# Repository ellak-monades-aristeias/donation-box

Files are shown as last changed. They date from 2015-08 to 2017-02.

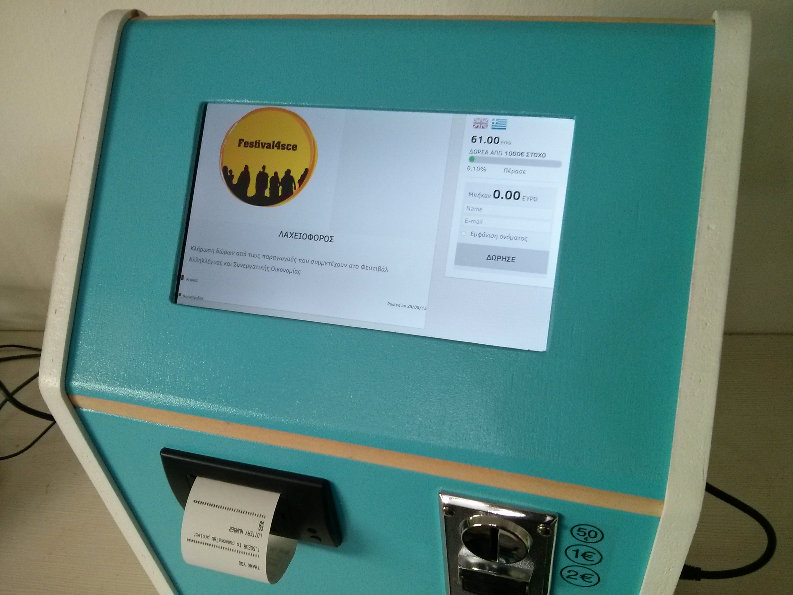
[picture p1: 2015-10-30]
info/photos/inuse/PrintedReceipt.jpg

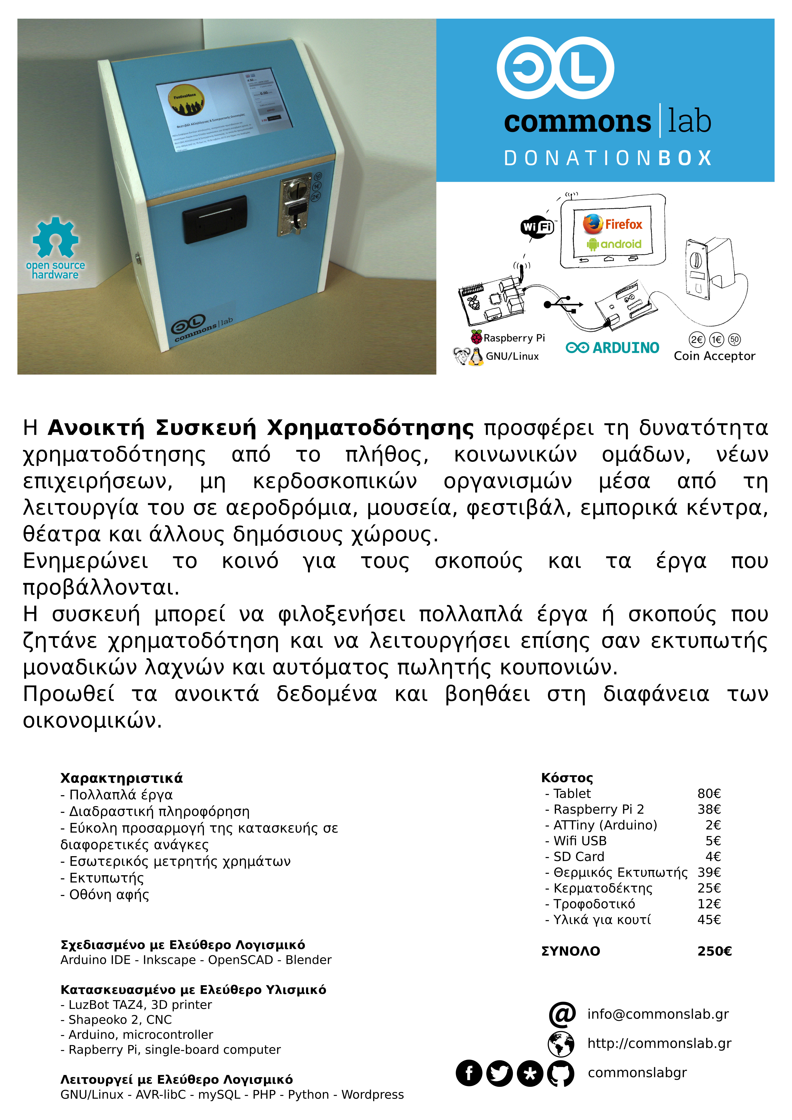
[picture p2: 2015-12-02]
info/Poster-el.jpg

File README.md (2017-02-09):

donation-box
============

open source design/ open source hardware/ open source software

Note: The process of how to set up your own donation box is still under heavy development and the documentation not complete or detailed enough yet. If you are anyhow interested in building and setting up your own box and you can't wait, don't hesitate to contact us.

##Idea
During the last few years, especially in Greece, many communities and initiatives have tried to do things in many different fields of interest. Often times, these teams will sooner or later need some funding in order to fulfill their goals. Some of them organize events, some run online crowdfunding campains and some also find several new ways to cover their needs.
From our experience, online crowdfunding does not work as expected, most of the time. People are hesitating to put all their details online, especially if they choose to donate a small amount, or some may not have a debit or credit card to do that. Eventually, most of these people prefer to give their donations in cash, in person or into a physical box somewhere. Of course, many donation boxes, usually managed by NGOs, already exist in public places, shops and such places. The problem with these boxes is that they do not offer much information about the organization that asks for money, nor do they offer transparency about what happens to the donations, who are the organization, or how much money they need.
Due to the lack of possible ways to convey sufficient information, traditional donation boxes are not being used by teams that focus on a specific project, because people can not understand what the project exactly is.
In order to solve the above problems, we came up with the idea of a screen-enabled interactive donation box.
The box can run several projects or causes that are asking for donations. It provides information (text, images, video) for each project. It provides real-time information about the progress (donations accepted, donations needed, finishing date). Donations are recorded and if users choose so, they can be registered to keep in touch with the project for which they donated.
The box also can issue receipts for each donation.
Connecting several donation boxes to an online service can add more value to each box and all the projects that are running, as a project can be created online and activated in several boxes in several locations simultaneously.
This way, we hope to help NGOs, social initiatives and others, to achieve their goals and their fulfil their ideas. By offering a platform for crowdfunding that exists in physical, public spaces, we are offering a different and more direct connection between projects asking for help and people willing to help.

##Description
An open-source screen enabled donation box

The software has three items. 
* The Serial2DB which is a simple deamon written in python which listens on the serial port for messages from the Arduino which is connected to the coin acceptor and writes all entries to an SQL DB.
* The wsServer which is a WebSocket server written in python which reads the SQL DB for new entries and then notifies any connected websocket clients of these. Additionally listens for any donations made and alters accordingly the SQL DB.
* The Wordpress widgets and theme customizations. Which are used for offering an improved user experience based on the design assumption that the wordpress site is running on a 10" tablet. The theme is currently based on Influence and there are several widgets developed to enhance the sidebar. Several plug ins needed for the current implementation and features are already under the plugins folder.

##Setup
###Hardware
The current development is based on the initial following design:
  *A programmable coint acceptor
  *Arduino compatible, connected to the coin acceptor and translating the readings to something more readable (e.g. EUR|2.00)
  *A Raspberry Pi connected through serial to the Arduino and running this software.
  *A tablet that connects through WiFi to the Raspberry Pi (that acts as a hot spot) and loads the Wordpress site.

###Installation
####Arduino
The code for the Arduino to read the coin acceptor will be uploaded soon...

####Raspberry Pi

* Set up DHCP
* Set up DNS
* Set up WiFi access point
* Set up IP forwarding
* Install python tornado
* [Printer] sudo apt-get install python-serial python-imaging python-unidecode
* Copy repository and start Serial2DB & wsServer.

* Install lighthttpd
* Install MySQL
* Create custom DB tables. Run the create_tables.sql
* Install PHP
* Set up Wordpress
* Add Influence theme 
* Add included child theme & plugins
* Import widgets 

####Android Tablet
* Install Firefox
* Connect to WiFi running on the Pi.
* Load home page
##Developers
More detailed [Developers Manual](DevelopersManual.md).

##Users
More detailed [Users Manual](UserManual.md).

Developed by CommonsLab

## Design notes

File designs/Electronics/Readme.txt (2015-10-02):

DonationBox.fzz
Contains the electronics schematic for the custom Raspberry Pi shield.
To open it you will need Fritzing - http://fritzing.org

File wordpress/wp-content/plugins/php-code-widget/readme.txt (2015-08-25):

=== PHP Code Widget ===
Contributors: Otto42
Donate link: https://www.paypal.com/cgi-bin/webscr?cmd=_donations&business=otto%40ottodestruct%2ecom
Tags: php, widget, execphp
Requires at least: 2.8
Tested up to: 4.3
Stable tag: 2.3
License: GPLv2
License URI: http://www.opensource.org/licenses/GPL-2.0

Like the Text widget, but also allows working PHP code to be inserted.

== Description ==

The normal Text widget allows you to insert arbitrary Text and/or HTML code. This allows that too, but also parses any PHP code in the text widget and executes it. 

This can make it easier to migrate to a widget-based theme. However, this plugin should not be used long term, as anybody with access to edit the widgets on your site will be able to execute arbitrary PHP code.

All PHP code must be enclosed in the standard php opening and closing tags ( `<?php` and `?>` ) for it to be recognized and executed.

Only users with the unfiltered_html role will be allowed to insert unfiltered HTML. This includes PHP code, so users without admin or editor permissions will not be able to use this to execute code, even if they have widget editing permissions.

== Frequently Asked Questions ==

= There's some kind of error on line 26! =

That error means that your PHP code is incorrect or otherwise broken. 

= But my code is fine! =

No, it's not. Really. 

This widget has no real errors in it, it's about the simplest widget one can possibly make. Any errors coming out of the "execphp.php" file are errors in code you put into one of the widgets. The reason that it shows the error being in the execphp.php file is because that is where your widget's code is actually being run.

So, if it says that you have an error on line 26, I assure you, the problem is yours. Please don't email me about that error.

= I have code that works normally in a template but doesn't work when in the widget? =

Code in a template runs in the global context. Code in the widget will run in a function context. Make sure that you declare any global variables as global before attempting to use them.

== Screenshots ==

1. The widgets screen showing a PHP code widget in use.
2. The output of the widget on the site.

== Changelog ==

= 2.3 =
* Changed the call to WP_Widget to use the PHP 5 __construct() method. Ref: https://make.wordpress.org/core/2015/07/02/deprecating-php4-style-constructors-in-wordpress-4-3/

= 2.2 =
* Translation fixes for WP 3.7
* Remove donation link

= 2.1 =
* Fixed broken wpautop filter. Checkbox on widget works now.

= 2.0 =
* Changed widget to use new Class methods for creating widget. This simplifies the widget and should eliminate any problems with it losing code or disappearing from sidebars and so forth.

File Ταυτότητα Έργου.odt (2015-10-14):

Ανοικτή Συσκευή Χρηματοδότησης Donation Box

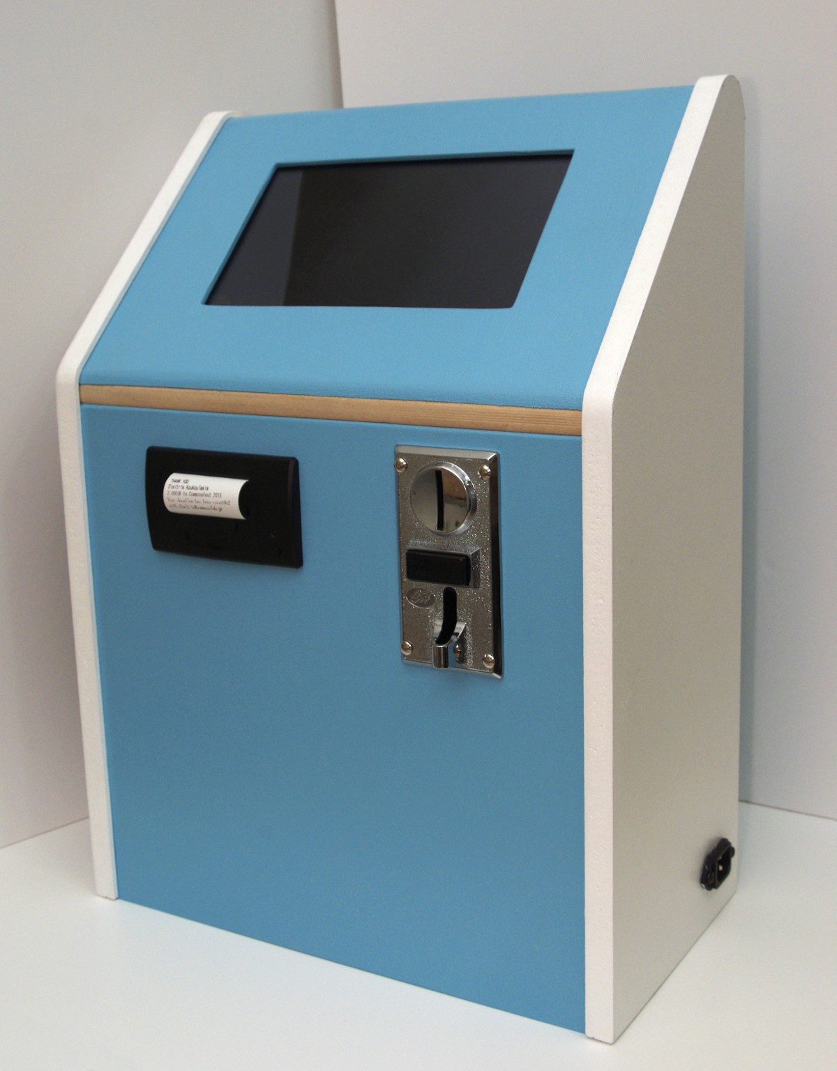
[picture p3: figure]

# Περιγραφή

Η Ανοικτή Συσκευή Χρηματοδότησης δίνει τη δυνατότητα χρηματοδότησης σε ομάδες και έργα μέσα από τη προβολή τους σε δημόσιους φυσικούς χώρους. Μπορεί να παρέχει πληροφορίες για κάθε ομάδα και έργο που ζητάει χρηματοδότηση, να δέχεται και να καταγράφει τα νομίσματα που δίνονται, να εκτυπώνει απόδειξη και να ενημερώνει τους χρήστες για τη πορεία χρηματοδότησης του κάθε έργου σε πραγματικό χρόνο.

# Χρήση

Η Ανοικτή Συσκευή Χρηματοδότησης έχει σκοπό τη διάδοση και υλοποίηση της ιδέας της χρηματοδότησης έργων από το πλήθος (crowdfunding) σε φυσικούς χώρους.

Η συσκευή μπορεί να εγκατασταθεί σε δημόσιους χώρους όπως μουσεία, πολιτιστικά κέντρα, καφετέριες, μεζεδοπωλεία, εμπορικά κέντρα, κοινωνικούς χώρους, αεροδρόμια κ.α.

Ο χρήστης μπορεί να επιλέγει τα έργα που θα εμφανίζονται για χρηματοδότηση και να κρατάει ένα ποσοστό αν έχει συμφωνηθεί για τη συντήρηση της συσκευής. Επίσης ο χρήστης ή κάποιος τρίτος να φροντίζει για τη σωστή διανομή των χρημάτων όπως θα έχει συμφωνηθεί. Τα ανοιχτά δεδομένα από τις συσκευές μπορούν να δημοσιεύονται στο διαδίκτυο ώστε μέσω της διαφάνειας να εξασφαλίζετε η διαδικασία.

# Υλικά

### Ξύλα

### Βίδες κ.α.

### Ηλεκτρονικά

ΣΥΝΟΛΟ 307,32 €

# Αποθετήριο

https://github.com/ellak-monades-aristeias/donation-box

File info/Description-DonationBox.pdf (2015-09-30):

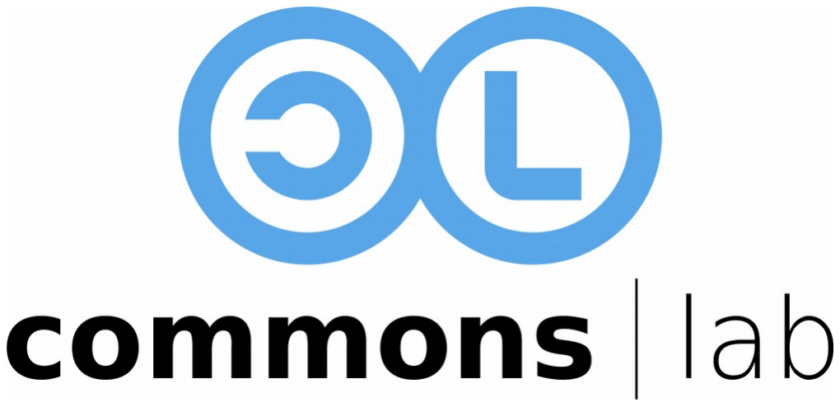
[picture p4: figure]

# Δίκτυο ανοικτών συσκευών μικροχρηματοδότησης

## Τεχνικά στοιχεία

Ανοικτός σχεδιασμός της συσκευής. Εύκολη αναπαραγωγή του και διαμόρφωση για να καλύψει τις ανάγκες σε διαφορετικούς χώρους.
Προσφέρει βασική ασφάλεια για τη συσκευή να βρίσκεται σε εσωτερικό δημόσιο χώρο. Περιλαμβάνει:
- ενα προγραμματιζόμενο κερματοδέκτη, για τουλάχιστον 3 διαφορετικά νομίσματα (0.50, 1.00 & 2.00 €)
- ένα μικροελεγκτή συμβατό με το Arduino
- ένα Raspberry Pi B (ή οποιοδήποτε άλλο Η/Υ που να τρέχει GNU/Linux)
- ένα WiFi usb stick.
- Τροφοδοτικό
- Ταμπλέτα 10”

Δίκτυο συσκευών
Δυνατότητα δημοσίευσης και παρακολούθησης των έργων σε διαδικτιακή εφαρμογή με την οποία επικοινωνούν, ενημερώνουν και ενημερώνονται οι συσκευές χρηματοδότησης σε όποιο σημείο και αν βρίσκονται.

## Σκοπός και χρήση

Η ανοικτή συσκευή οικονομικής ενίσχυσης έχει σαν σκοπό την διάδοση και την υλοποίηση της ιδέας της χρηματοδότησης έργων από το πλήθος (crowdfunding) σε φυσικούς χώρους.

## Υπάρχουσες λύσεις

Η χρηματοδότηση από το πλήθος τα τελευταία χρόνια έχει δώσει την δυνατότητα σε χιλιάδες άτομα, ομάδες, οργανισμούς και επιχειρήσεις από όλο τον κόσμο να έχουν πρόσβαση σε χρηματικά κεφάλαια προκειμένου να υλοποιούν πάσης φύσεως έργα.

Αυτό επιτυγχάνεται μέσα από διάφορες ηλεκτρονικές πλατφόρμες οπού οι ενδιαφερόμενοι παρουσιάζουν τις ιδέες τους στο κοινό και ζητάνε συγκεκριμένα ποσά για την υλοποίηση τους. Οι χρηματοδότες με την χρήση λογαριασμών PayPal ή χρεωστικών και πιστωτικών καρτών ενισχύουν οικονομικά τα διάφορα έργα.
Την ίδια στιγμή σε δημόσιους χώρους υπάρχουν κουτιά οικονομικής ενίσχυσης που τοποθετούν διάφορες ομάδες ή μη κερδοσκοπικές οργανώσεις προκειμένου να ενισχύσουν δράσεις φιλανθρωπικού, καλλιτεχνικού, κοινωνικά αλληλέγγυου κ.α. χαρακτήρα.
Τα συγκεκριμένα κουτιά ενίσχυσης στηρίζονται κατά κύριο λόγο στην εμπιστοσύνη που έχει το πλήθος προς την επωνυμία του κατόχου τους χωρίς όμως να δίνουν οποιαδήποτε άλλη πληροφορία σχετικά με το έργο,την ομάδα, το πόσο που έχει συγκεντρωθεί σε κάθε χρονική στιγμή και το πόσο στόχο.

## Στοιχεία κοινοτομίας, ανάγκες και προβλήματα που επιλύει

Η συσκευή ανοικτής οικονομικής ενίσχυσης έχει σαν στόχο να καλύψει το κενό ανάμεσα στις δυο παραπάνω περιπτώσεις. Δίνοντας την δυνατότητα στους ενδιαφερόμενους:
- Να παρουσιάσουν την ομάδα και το έργο τους μέσα από κείμενα, φωτογραφίες, βίντεο.
- Να παρέχουν πρόσβαση στα οικονομικά δεδομένα του ποσού στόχου και του ποσού που έχει συγκεντρωθεί.
- Να συγκεντρώσουν ποσά που οι ενδιαφερόμενοι μικροχρηματοδότες δεν θα έδιναν σε πλατφόρμες crowdfunding λόγω της διαδικασίας υποβολής των προσωπικών στοιχείων που απαιτούνται.
- Να έχουν πρόσβαση σε ένα μεγαλύτερο δίκτυο συσκευών μικροχρηματοδότησης που εκτείνεται και πέρα από τα γεωγραφικά όρια δράσης τους.
- Να παρέχουν πληροφορίες για την πορεία υλοποίησης του έργου
- Να καλλιεργούν το προφίλ τους μέσα στο ευρύτερο δίκτυο.
- Να κατασκευάσουν μόνοι τους την συσκευή οικονομικής ενίσχυσης κάνοντας χρήση των ελεύθερων αδειών λογισμικού, υλισμικού και σχεδιασμού.

## Οφέλη ανοιχτότητας - Σύντομη τεκμηρίωση της κοινωνικής, περιβαλλοντικής και οικονομικής

βιωσιμότητας της πρότασης.

Το γεγονός ότι η ανοικτή συσκευή οικονομικής ενίσχυσης καλύπτεται από ελεύθερες άδειες λογισμικού, υλισμικου και σχεδίασης έχει τα εξής οφέλη
ως προς την κατασκευή:
1. Την δυνατότητα κατασκευής της από οποιονδήποτε το επιθυμεί.
2. Την δυνατότητα αναβάθμισης, προσαρμογής και βελτίωσης της.
Ως προς την κοινωνική βιωσιμότητα:
1. Την δυνατότητα πρόσβασης σε μικροχρηματοδότηση έργων που δεν μπορούν να χρηματοδοτηθούν με άλλο τρόπο.
2. Με την χρήση ανοικτών δεδομένων ελαχιστοποιείται η πιθανότητα παραπλάνησης όσων θέλουν να ενισχύσουν και την καλλιέργεια σχέσεων εμπιστοσύνης μειώνοντας έτσι τους πόρους που απαιτούνται για το σκοπό αυτό σε μεταγενέστερη πρόταση χρηματοδότησης.
3. Την ενίσχυση της ιδέας της κοινότητας και την παροχή δυνατότητας συμμετοχής σε έργα με κοινωνικό όφελος μέσω της χρηματοδότησης από άτομα που δεν έχουν τον χρόνο να συμμετέχουν με άλλο τρόπο.
Ως προς την περιβαλλοντική βιωσιμότητα
- Η κατασκευή της συσκευής μπορεί να γίνει με την χρήση μηχανημάτων μικρής όχλησης χωρίς να απαιτεί ιδιαίτερες εγκαταστάσεις και λόγω των ελεύθερων αδειών της μπορεί να στηριχθεί σε ένα ομότιμο δίκτυο παραγωγής και διαχείρισης σε τοπικό επίπεδο.
Το δίκτυο αυτό θα έχει την δυνατότητα μέσω της χρήσης ήδη τοποθετημένων συσκευών ενίσχυσης να χρηματοδοτεί την κατασκευή και την τοποθέτηση νέων συσκευών δημιουργώντας έτσι τις προϋποθέσεις περαιτέρω επέκτασης του. Ουσιαστικά μια συσκευή έχει την δυνατότητα χρηματοδότησης μιας νέας συσκευής.
- Δίνει την δυνατότητα μείωσης του κόστους κατασκευής και λειτουργίας με την χρήση laptop, tablet, touchscreen, smartphone και δικτύων wifi που υπάρχουν ήδη.

Τέλος η συσκευή ενίσχυσης με την τοποθέτηση της σε δημόσιο χώρο μπορεί να έχει και άλλες χρήσεις εκτός της μικροχρηματοδοτησης όπως:
- Αγορά ψηφιακών νομισμάτων
- Παροχή πάσης φύσεως πληροφορίας
- Διοργάνωση κληρώσεων δώρων
- Αυτόματου πωλητή μέσω κουπονιών
- Παροχή wifi

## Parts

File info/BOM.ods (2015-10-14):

Donation Box Bill of Materials
Items | Description | Notes | Cost | Source
Case
 | MDF | 8mm ca. 1m2 | 8,00 € | Praktiker
 | Plywood | 4mm ca. 1/4m2 | 3,00 € | Praktiker
 | Chipboard | 16mm ca. 1m2 | 8,00 € | Praktiker
 | Power off Button |  | 0,50 € | Local electronics store
 | Hinge | 2x | 4,00 € | Praktiker
 | Screws & Nuts |  | 4,00 € | Local Hardware store
 |  | 40x 3mmx16mm |  | Local Hardware store
 |  | 4x M4 20mm
 |  | 4x M4
 | Angles | 12x | 3,60 €
 | Lock | D19XL22 | 9,00 € | Local Hardware store
Electronics
1 | Raspberry Pi 2 |  | 37,50 € | http://www.reichelt.com/?ARTICLE=152728
1 | Coin Acceptor |  | 25,00 € | http://www.ebay.com/itm/250784120899
1 | Arduino | ATtiny85 | 1,20 € | http://www.reichelt.com/?ARTICLE=69299
1 | Power supplies | 12V 0.5A | 2,00 €
 |  | 9V 1.5A | 2,00 €
 |  | 5V 2A | 2,00 €
 |  | 5V 1.5A | 2,00 €
1 | Wifi dongle |  | 12,00 € | http://www.aliexpress.com/item/Free-Shipping-Mini-150M-Networking-Cards-Wireless-Wifi-802-11-n-g-b-Computer-Accessories-High/1506557627.html
1 | 10” Android Tablet | Bitmore 1022Q | 150,41 € | http://cosmodata.gr
1 | Thermal printer |  | 39,00 € | http://www.aliexpress.com/item/58mm-Embedded-Thermal-Receipt-Printer-Mini-Panel-Printer/32328915173.html
1 | SD card |  | 3,11 € | http://www.cosmodata.gr/product/4799/
TOTAL |  |  | 316,32

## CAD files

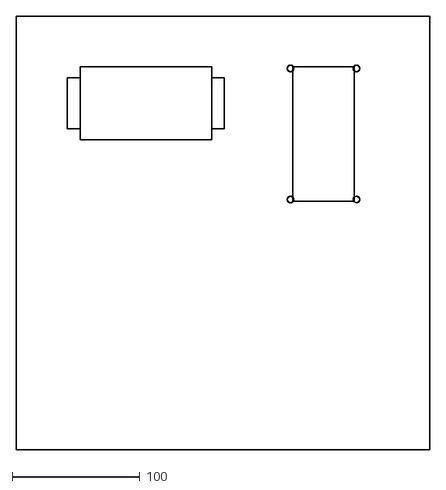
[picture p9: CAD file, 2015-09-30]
designs/3D/openscad/front_panel.dxf
323.5 x 339.4

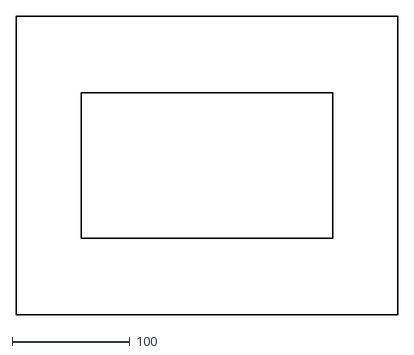
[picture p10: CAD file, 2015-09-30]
designs/3D/openscad/tablet-top.dxf
323.9 x 253.4

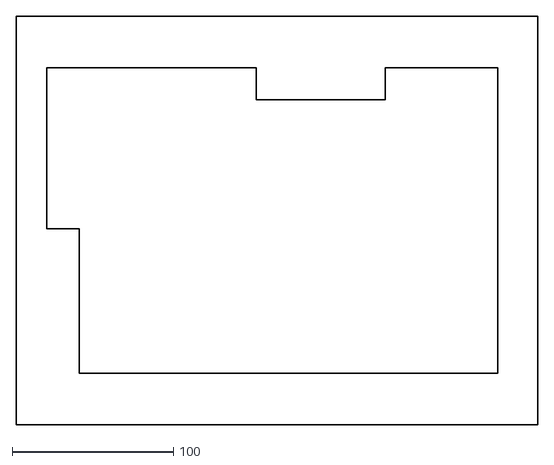
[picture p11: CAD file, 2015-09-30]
designs/3D/openscad/tablet-side-support.dxf
323.9 x 253.4

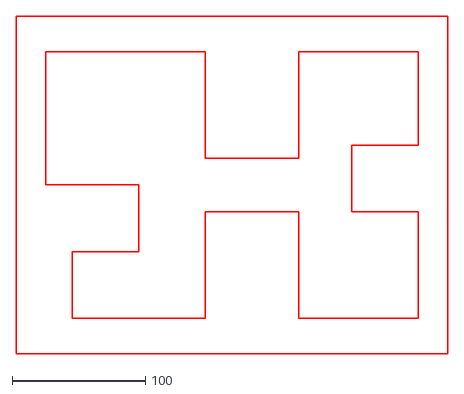
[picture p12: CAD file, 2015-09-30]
designs/3D/openscad/tablet-bottom-support.dxf
323.9 x 253.4

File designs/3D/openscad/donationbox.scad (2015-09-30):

/* 3D representation of Donation Box
*  
* Description: A 3D model of the initial version of Donation Box. The design include the tablet casing, the thermal printer and coin acceptor cuts. Details are not included.
*
* Author: Commonslab.gr
* License: CC-BY-SA v4.0 
*/

/*Set Themes*/
theme = "greek island"; //"attention";

surface_color = theme=="greek island" ? "RoyalBlue" : "OrangeRed";
side_color = theme=="greek island" ? "White" : "DarkSlateGray";

tablet_color ="Black";
tablet_back_color="Black";


module side_panel(h)
{
    color(side_color)
  scale([25.4/90, -25.4/90, 1]) union()
  {
    linear_extrude(height=h)
      polygon([[319.029295,-974.355450],[314.679432,-973.939007],[310.458314,-972.963828],[306.384014,-971.438098],[302.544942,-969.391321],[299.021511,-966.870154],[295.832035,-963.882850],[289.023977,-956.600953],[282.215482,-949.318588],[275.407413,-942.036679],[268.598413,-934.753775],[261.789307,-927.470756],[254.980939,-920.188527],[248.171642,-912.905305],[241.363305,-905.623109],[234.554502,-898.340415],[227.746157,-891.058211],[220.937034,-883.775174],[214.128652,-876.492931],[207.320120,-869.210526],[200.511764,-861.928310],[193.703336,-854.646017],[186.894858,-847.363671],[180.086214,-840.081147],[173.277629,-832.798685],[166.468953,-825.516128],[159.659941,-818.233210],[152.851555,-810.950962],[146.042875,-803.668399],[139.234505,-796.386168],[132.425406,-789.103157],[125.616278,-781.820116],[118.807447,-774.537391],[111.998923,-767.254995],[105.190460,-759.972666],[98.381608,-752.689918],[91.572839,-745.407261],[84.764491,-738.125054],[77.955724,-730.842398],[71.146715,-723.559483],[64.338657,-716.277587],[57.529534,-708.994550],[50.720528,-701.711639],[43.911776,-694.429000],[37.102428,-687.145722],[30.293767,-679.863180],[23.485092,-672.580623],[16.675834,-665.297442],[9.867542,-658.015294],[3.058906,-650.732779],[-3.749237,-643.450790],[-10.557822,-636.168330],[-17.366598,-628.885664],[-24.175111,-621.603281],[-30.983607,-614.320915],[-37.792960,-607.037632],[-44.601929,-599.754761],[-51.410783,-592.472012],[-58.219437,-585.189478],[-65.027440,-577.907639],[-71.835634,-570.625596],[-78.644362,-563.342983],[-85.452664,-556.060824],[-92.261482,-548.778113],[-99.070349,-541.495352],[-105.879711,-534.212059],[-112.687837,-526.930089],[-119.496699,-519.647332],[-126.305882,-512.364232],[-133.114110,-505.082152],[-139.923227,-497.799123],[-146.732507,-490.515919],[-153.541344,-483.233188],[-160.350290,-475.950340],[-167.158346,-468.668445],[-173.967517,-461.385358],[-180.775487,-454.103555],[-187.584495,-446.820641],[-194.393065,-439.538197],[-201.202115,-432.255238],[-208.010263,-424.973244],[-214.819073,-417.690543],[-221.627435,-410.408321],[-228.436147,-403.125724],[-235.244852,-395.843134],[-242.053874,-388.560206],[-248.862344,-381.277868],[-255.671515,-373.994781],[-262.480111,-366.712308],[-269.289174,-359.429335],[-276.098318,-352.146276],[-282.906760,-344.863968],[-289.714668,-337.582232],[-296.523366,-330.299650],[-303.332344,-323.016769],[-310.140803,-315.734442],[-316.949991,-308.451337],[-323.758120,-301.169363],[-330.567011,-293.886575],[-337.375590,-286.604120],[-344.183595,-279.322280],[-346.827888,-276.111048],[-349.032827,-272.621875],[-350.792525,-268.869720],[-352.069664,-264.927118],[-352.841979,-260.872435],[-353.103515,-256.720720],[-353.103515,-246.737852],[-353.103515,-236.754129],[-353.103515,-226.770934],[-353.103515,-216.787561],[-353.103515,-206.804260],[-353.103515,-196.821059],[-353.103515,-186.838536],[-353.103515,-176.855324],[-353.103515,-166.872553],[-353.103515,-156.889702],[-353.103515,-146.906390],[-353.103515,-136.923699],[-353.103515,-126.941378],[-353.103515,-116.958674],[-353.103515,-106.976266],[-353.103515,-96.994010],[-353.103515,-87.009990],[-353.103515,-77.026982],[-353.103515,-67.043535],[-353.103515,-57.060108],[-353.103515,-47.077527],[-353.103515,-37.095272],[-353.103515,-27.111657],[-353.103515,-17.128026],[-353.103515,-7.144922],[-353.103515,2.837811],[-353.103515,12.820944],[-353.103515,22.803735],[-353.103515,32.787934],[-353.103515,42.771589],[-353.103515,52.755131],[-353.103515,62.739282],[-353.103515,72.722966],[-353.103515,82.705326],[-353.103515,92.687741],[-353.103515,102.671740],[-353.103515,112.654902],[-353.103515,122.639000],[-353.103515,132.621830],[-353.103515,142.605324],[-353.103515,152.589434],[-353.103515,162.572156],[-353.103515,172.555525],[-353.103515,182.539573],[-353.103515,192.522367],[-353.103515,202.505914],[-353.103515,212.488270],[-353.103515,222.471361],[-353.103515,232.455106],[-353.103515,242.437469],[-353.103515,252.420183],[-353.103515,262.402981],[-353.103515,272.385523],[-353.103515,282.369222],[-353.103515,292.351689],[-353.103515,302.334120],[-353.103515,312.317539],[-353.103515,322.301023],[-353.103515,332.283533],[-353.103515,342.267383],[-353.103515,352.251184],[-353.103515,362.233422],[-353.103515,372.215805],[-353.103515,382.199745],[-353.103515,392.183093],[-353.103515,402.166782],[-353.103515,412.149848],[-353.103515,422.132666],[-353.103515,432.116840],[-353.103515,442.100515],[-353.103515,452.083103],[-353.103515,462.066641],[-353.103515,472.049744],[-353.103515,482.032127],[-353.103515,492.014478],[-353.103515,501.996962],[-353.103515,511.980570],[-353.103515,521.964332],[-353.103515,531.948053],[-353.103515,541.932188],[-353.103515,551.915204],[-353.103515,561.898621],[-353.103515,571.881821],[-353.103515,581.864528],[-353.103515,591.847821],[-353.103515,601.831637],[-353.103515,611.814775],[-353.103515,621.797029],[-353.103515,631.780985],[-353.103515,641.763440],[-353.103515,651.745736],[-353.103515,661.729137],[-353.103515,671.712731],[-353.103515,681.697004],[-353.103515,691.679868],[-353.103515,701.663309],[-353.103515,711.647473],[-353.103515,721.630433],[-353.103515,731.613833],[-353.103515,741.597241],[-353.103515,751.580344],[-353.103515,761.564408],[-353.103515,771.548167],[-353.103515,781.531405],[-353.103515,791.514898],[-353.103515,801.497618],[-353.103515,811.481655],[-353.103515,821.465307],[-353.103515,831.448642],[-353.103515,841.431598],[-353.103515,851.414839],[-353.103515,861.397375],[-353.103515,871.380402],[-353.103515,881.363797],[-353.103515,891.346885],[-353.103515,901.329165],[-353.103515,911.312853],[-353.103515,921.296215],[-353.103515,931.279647],[-353.103515,941.261700],[-352.816875,945.631696],[-351.982594,949.828971],[-350.581439,953.951624],[-348.672946,957.810326],[-346.259911,961.413610],[-343.408127,964.661999],[-340.159359,967.513686],[-336.555694,969.926539],[-332.697035,971.834590],[-328.574485,973.235313],[-324.377484,974.069176],[-320.007815,974.355450],[-310.161031,974.355450],[-300.314646,974.355450],[-290.468112,974.355450],[-280.621565,974.355450],[-270.775304,974.355450],[-260.928875,974.355450],[-251.083079,974.355450],[-241.236310,974.355450],[-231.389788,974.355450],[-221.542735,974.355450],[-211.696755,974.355450],[-201.850628,974.355450],[-192.003543,974.355450],[-182.157429,974.355450],[-172.312002,974.355450],[-162.465803,974.355450],[-152.619223,974.355450],[-142.772917,974.355450],[-132.926055,974.355450],[-123.078894,974.355450],[-113.233049,974.355450],[-103.387350,974.355450],[-93.540277,974.355450],[-83.694414,974.355450],[-73.847986,974.355450],[-64.001458,974.355450],[-54.155480,974.355450],[-44.308978,974.355450],[-34.463370,974.355450],[-24.616628,974.355450],[-14.769454,974.355450],[-4.923303,974.355450],[4.923268,974.355450],[14.770535,974.355450],[24.617547,974.355450],[34.463807,974.355450],[44.310704,974.355450],[54.157756,974.355450],[64.004164,974.355450],[73.850099,974.355450],[83.696214,974.355450],[93.543132,974.355450],[103.389544,974.355450],[113.236001,974.355450],[123.081304,974.355450],[132.926987,974.355450],[142.773377,974.355450],[152.619711,974.355450],[162.466102,974.355450],[172.312466,974.355450],[182.158109,974.355450],[192.005170,974.355450],[201.851264,974.355450],[211.697363,974.355450],[221.543972,974.355450],[231.390644,974.355450],[241.236717,974.355450],[251.082284,974.355450],[260.928301,974.355450],[270.774493,974.355450],[280.621468,974.355450],[290.468029,974.355450],[300.315289,974.355450],[310.161999,974.355450],[320.007815,974.355450],[324.377828,974.069052],[328.575151,973.235007],[332.697888,971.834089],[336.556701,969.925822],[340.160128,967.513000],[343.408684,964.661412],[346.260562,961.412817],[348.673627,957.809301],[350.581906,953.950761],[351.982873,949.828299],[352.816983,945.631351],[353.103515,941.261700],[353.103515,931.300766],[353.103515,921.340330],[353.103515,911.379727],[353.103515,901.419697],[353.103515,891.460141],[353.103515,881.499304],[353.103515,871.539334],[353.103515,861.578376],[353.103515,851.617358],[353.103515,841.656162],[353.103515,831.695699],[353.103515,821.735663],[353.103515,811.775266],[353.103515,801.813807],[353.103515,791.852883],[353.103515,781.892952],[353.103515,771.933014],[353.103515,761.972693],[353.103515,752.012969],[353.103515,742.052596],[353.103515,732.0
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

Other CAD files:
designs/3D/blender/back panel/back panel.blend
designs/3D/blender/back panel/door-hinge-blocks.blend
designs/3D/blender/back panel/rounding-gap.blend
designs/3D/blender/bottom panel/bottom panel.blend
designs/3D/blender/front panel/front panel.blend
designs/3D/blender/left-side panel/door.blend
designs/3D/blender/left-side panel/left-side panel.blend
designs/3D/blender/right-side panel/right-side panel.blend
designs/3D/blender/top panel/top panel.blend

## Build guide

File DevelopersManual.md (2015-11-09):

donation-box
============

open source design/ open source hardware/ open source software

##Software Development
The current software stack of donation box consists of:
        Coin Acceptor Interface
        Serial deamon
        MySQL tables
        WebSocket Server
        Wordpress customization
        
###Coin Acceptor Interface
A simple Arduino code that reads the pulses from the coin acceptor and interprets them to a readable string that is send through the serial. 
For example:
        1 pulse = EUR0.50
        2 pulses = EUR1.00
        4 pulses = EUR2.00

The interface follows the ISO 4217 3 letter code for currencies followed by the value of the coin.

The currency used is defined in the code along with the coins.
The code can run in any Arduino compatible hardware, like the ATTiny, UNO etc.

Files:
        ```
        ATTiny
        arduino/ch_92x_interface_attiny/ch_92x_interface_attiny.ino
        arduino/ch_92x_interface_attiny/notes.h
        Arduino UNO
        arduino/ch_92x_interface_ardu/ch_92x_interface_ardu.ino
        arduino/ch_92x_interface_ardu/notes.h        
        ```

###Serial deamon
A simple deamon in Python that reads on the Serial port, what is send from the Coin Acceptor Interface, (e.g. EUR1.00) and writes the value and currency to the MySQL table "coinacceptor".

Newly insersted coins are inserted to the table with donationid=-1.

Files:
        ```
        Serial2DB.py
        ```
        
###WebSocket Server
A simple deamon in Python that acts as a WebSocket Server communicating with the browser to inform the user of inserted coins and also record donations.
Has two threads, one which is polling the MySQL table "coinacceptor" for new inserted coins which are identified if donationid=-1.
The other thread is the WebSocket server, which hanldes all communication with the browser.
  Sends information about new coins inserted.
  Receives donation and writes the donation information to the "donations" (name,email,project,amount,currency) database table. Gets the donationid given and updates the "coinacceptor" entries with that donationid to mark the coins as donated.
  Prints receipt using the Adafruit_Thermal.py library.

Files:
        ```
        wsServer.py
        ```
###Wordpress customization
The Wordpress includes the installation of the following plugins and further customization is done by widgets and in the header.php file.
Plugins:
        master-slider For having a touch enabled slideshow home screen when displaying multiple projects
        php-code-widget For having php code in some widgets
        qtranslate-x-master For enabling multilingual support on the widgets and on the content
        widget-importer-exporter to easily import & export the widgets
        
####header.php
The main aspect of the added code in the header.php is for the WebSocket client, in Javascript, which updates the UI when new coins are inserted and sends the data to the WebSocket server when the donation button is clicked.
It also has a timer for redirecting the browser to the home page when the donation box is running multiple projects.

####Widgets
- Language Selector widget
- Total amount raised
- Progress Bar
- Days Left
- Donation form
- Home Button
- Info pop up Button
        
Files:
        ```
        wordpress/wp-content/themes/influence-child/header.php
        wordpress/wp-content/themes/influence-child/style.css
        wordpress/donationbox.pi-widgets.wie
        ```
        
##Hardware Development
The hardware is the following:
        Programmable Coin Acceptor
        Arduino compatible microcontroller
        Raspberry Pi 2 + Wifi USB for Access Point
        Tablet

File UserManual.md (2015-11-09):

donation-box
============

open source design/ open source hardware/ open source software

##Installation
The installation of a donation box contains the assembly of the box and connecting the electronic components.

###Assembling the box
1. Start by putting one of the side pieces flat on a surface with the grooves on top.
2. Screw the angles for the bottom, back and front panels.
3. Place the bottom, front and back panels and screw them on the angles
4. Put lock and hinges on door.
5. Put Raspberry Pi and shield on place and screw it.
6. Prepare SD card and place it in Raspbery Pi
7. Connect USB Wifi dongle to Raspberry Pi .
8. Put coin acceptor in place and connect cable on the shield.
9. Put thermal printer in place and connect cable on the shield.
10. Place tablet and secure it in place.
11. Put power supply and connect to shield, Raspberry Pi and tablet.
12. Put box for falling coins in place.

##Turning on Donation Box
Make sure power supply, thermal printer, coin acceptor are connected.
Then plug in power. Raspberry Pi will turn on and boot automatically.
Wait for about 2 minutes and then turn on the tablet and look for the DonationBox Wifi.
Once connected go to Firefox browser and go to http://donationbox.pi URL. 

##Adding new project
This can be done from the tablet but it will be easier if you connect to the DonationBox Wifi from a laptop/PC.
1. Go to http://donationbox.pi/wp-admin URL and log in.
2. Create new Post.
3. Edit post and upload a featured image. Select category "Project" for post. 
4. Publish post.

##Home page
If you want to run the donation box for a single project then just set the post as home page from the theme customizer.
When setting the donation box for running multiple projects you need to create a page and set it as home page.
Set up a slider using the master slider plug in and place this slider on the page created and set as home.

NOTE: Configuring the box for single or multiple projects has to be set currently in several places (header.php & widgets).
Soon the process will be updated and simplified.

##Troubleshooting
Coming soon

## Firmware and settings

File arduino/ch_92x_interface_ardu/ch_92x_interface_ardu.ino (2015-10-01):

/*
    ch_92x_interface.ino - CH-92x coin acceptor interface (AGPL3+)

    This sketch interfaces a CH-92x series coin acceptor device.
    It waits for pulses on a digital input pit and then sends
    clear-text information accordingly through any output pin 
    via SoftwareSerial.

    Copyright (C) 2014  
    by Jann Eike  Kruse,  Dimitris  Koukoulakis,  Manolis Britsolakis

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
    You should have received a copy of the GNU Affero General Public License
    along with this program.  If not, see <http://www.gnu.org/licenses/>.
*/

/* VERSION HISTORY
*********************

2014-06-18  Jann Kruse
v. 0.1      First draft

2014-06-23  Jann Kruse
v. 0.2      Start implementing finite state machine.

2014-06-24  Jann Kruse
v. 0.3RC    Basic features are there. Ready for release after some clean-up.

*/


// coin   1c  2c  5c 10c 20c 50c 1€  2€
// pulses 3   5   7   9  11  13  15  17

//#include <SoftwareSerial.h>
#include "notes.h"

const char* CURRENCY = "EUR";   // Currency unit of the coin acceptor
const int   MAX_PULSES = 99;    // Not more that so many pulses make sense. Stop counting here and complain.
const int   centPerPulse = 50;  // This many 1/100th of a currency unit are counted per pulse.

// Define here some timing constants according to the settings of the coin acceptor.
enum timing
  {
    T_MIN = 25,     // The PULSE_INPUT shourd be LOW or HIGH for at least this long, otherwise it's noise.
    T_MAX = 150,    // The PULSE_INPUT shourd be LOW or HIGH for at most this long, otherwise it's not a pulse.
  };


// Define here how the Arduino (or ATtiny) is connected.
enum cabling
  {
    STATUS_LED   = 2,  // You may connect the status LED here.         (ATtiny85 DIP pin 5 - TX+LED on Arduino)
    PULSE_INPUT  = 3,  // Connect the coin acceptor's COIN output here.(ATtiny85 DIP pin 6 - RX+LED on Arduino)
    SPEAKER      = 4,  // You may connect a beeper/speaker here.       (ATtiny85 DIP pin 7)
    SERIAL_RX    = 5,  // Serial data input from the other Arduino/PC. (ATtiny85 DIP pin 2)
    SERIAL_TX    = 6,  // Serial data output to the other Arduino/PC.  (ATtiny85 DIP pin 3)
    ON_BOARD_LED = 13, // Most Arduino boards have LED here.           (default: Arduino pin 13)
  };


// States of the finite state machine:
enum state 
  {
  // The first (negative) states are initial, before the pulse sequence starts.
    INIT          = -1, // state after power-up, reset, or after reporting a pulse sequence.
    START         = -2, // Start here wating for a pulse.
    START_CONFIRM = -3, // Input just went HIGH for the first time.

  // The next (positive) states are to count the pulses in the sequence.
    LO            =  0, // Counting pulses, input pin is LOW  (0 V).
    HI            =  1, // Counting pulses, input pin is HIGH (5 V).
    LO_CONFIRM    =  2, // Counting pulses, input pin just went LOW.
    HI_CONFIRM    =  3, // Counting pulses, input pin just went HIGH.
  };

// Enable or disable debugging features here.
const boolean DEBUG = false;
const boolean VERBOSE = false;

//SoftwareSerial Serial(SERIAL_RX, SERIAL_TX); // Use software serial for compatibility with ATtiny85.

// Variables
unsigned char pulses; // Holds the number of pulses that have been counted lately. 
unsigned long tLow;  // Holds the millis() when pin went LOW.
unsigned long tHigh;    // Holds the millis() when pin went HIGH.
state currentState;   // Holds the current state of the finite state machine.

// This routine reports an error.
void reportError(int error) {
  switch (error) {
    default:
      beep(SPEAKER, 2000, 1000); // Beep for a second at 2kHz.
      if (VERBOSE) {Serial.print("Error: ");Serial.println(error);}

  };
};

// This routine reports counted pulses as coins through a serial connection.
void reportPulses(unsigned int pulses) {

  if (VERBOSE) {Serial.print("Reporting pulses: ");Serial.println(pulses);}

  Serial.print(CURRENCY);
  if (pulses*centPerPulse < 100)    Serial.print("0");
  else                              Serial.print(pulses*centPerPulse/100); // 100s (full units of the currency)
                                    Serial.print(".");
  if (pulses*centPerPulse%100 < 10) Serial.print("0");
                                    Serial.println(pulses*centPerPulse%100); // (10s and) 1s
};

// This function oscillates the given pin for the given time with the given frequency.
// This function is blocking (not like the Arduino tone() function).
void beep(char pin, unsigned int frequency, unsigned int milliseconds) {
  // Minimal frequency = 30Hz
  // Maximal frequency = 20kHz
  // Maximal duration = 65535 miliseconds = 65 seconds = 1 minute
  if (frequency < 30) frequency = 30;
  if (frequency > 20000) frequency = 20000;
  unsigned long cycles = ((unsigned long)frequency * milliseconds) / 1000 ; // cycles = frequency * seconds
  unsigned int half_period = 500000 / frequency; // half_perion = 1/2 * second / frequency
  for (unsigned long cycle = 0; cycle < cycles; cycle++) {
    digitalWrite(pin, HIGH);
    delayMicroseconds(half_period);
    digitalWrite(pin, LOW);
    delayMicroseconds(half_period);
  };
};


// the setup routine runs once when you power-up the Arduino or press reset:
void setup() {
  Serial.begin(9600); // Use previously defined pins to communicate at this baud rate.
  currentState = INIT;
};

// the loop routine runs over and over again forever:
void loop() {
  
  switch (currentState) {

    case INIT:
    // ENTRY:
      pulses = 0;
      if (VERBOSE) Serial.println("INIT");

      // Initialize digital pins.
      pinMode(ON_BOARD_LED, OUTPUT);
      pinMode(STATUS_LED,   OUTPUT);
      pinMode(SPEAKER,      OUTPUT);
      pinMode(PULSE_INPUT,  INPUT);
//      digitalWrite(PULSE_INPUT, HIGH); // Activate internal pull-up resistor. (So it's HIGH if not connected.)
      digitalWrite(PULSE_INPUT, LOW); // Dectivate internal pull-up resistor. (So it's not HIGH when idle.)
      digitalWrite(STATUS_LED, HIGH);  // Show, we're online...

    // WAIT FOR EVENT:
      while (not (digitalRead(PULSE_INPUT) == HIGH)) {}; // Wait for pin to go HIGH.
      // EVENT HAPPENED! PIN WENT HIGH.

    //EXIT:
      tHigh = millis();
      currentState = START;
    break;

    //---------------------------------------------
    case START:
    //ENTRY:
      if (VERBOSE) Serial.println("S");

    // WAIT FOR EVENT:
      while (digitalRead(PULSE_INPUT) == HIGH) {}; // Wait until pin goes LOW. (I.e. wait while pin stays HIGH.)
      // EVENT HAPPENED! PIN WENT LOW.

    //EXIT:
      currentState = START_CONFIRM;
    break;

    //---------------------------------------------
    case START_CONFIRM:
    //ENTRY:
      tLow = millis(); // Save system time when pin went LOW.
      if (VERBOSE) Serial.println("SC");

    // WAIT FOR EVENT:
      while (   (digitalRead(PULSE_INPUT) == LOW) // Wait until pin goes HIGH. (Wait while pin stays LOW.)
             && (millis() - tLow <= T_MIN)) {}; // as long as time reaches minimum (confirmed LOW).
      // EVENT HAPPENED! Either the pin went HIGH again quickly (noise?) or it's a stable LOW, i.e. a pulse.

    //EXIT:
      if (millis() - tLow >= T_MIN) { // Good pulse...probably. 
        currentState = LO;
      } else {
        currentState = START;             // Bad pulse... Back to START.
      }
    break;

    //---------------------------------------------
    case LO:
    //ENTRY:
      if (DEBUG) digitalWrite(STATUS_LED, LOW);
      if (VERBOSE) Serial.println("L");

    // WAIT FOR EVENT:
      while (   (digitalRead(PULSE_INPUT) == LOW)    // Wait while pin is stays LOW
             && (millis() - tLow <= T_MAX)) {}; // as long as time does not exceed maximum.
      // EVENT HAPPENED! Either the pin went HIGH again (end of pulse or noise) or something's wrong...

    //EXIT:
      if (millis() - tLow >= T_MAX) { // This is wrong... 
        reportError(millis() - tLow);
        currentState = INIT;
      } else {
        currentState = HI_CONFIRM;
      }
    break;

    //---------------------------------------------
    case HI_CONFIRM:
    //ENTRY:
      tHigh = millis(); // Save system time when pin went HIGH.
      if (VERBOSE) {Serial.print("HC -");Serial.println(millis() - tLow);}

    // WAIT FOR EVENT:
      while (   (digitalRead(PULSE_INPUT) == HIGH)   // Wait until pin goes LOW (while pin is stays HIGH)
             && (millis() - tHigh <= T_MIN)) {};  // as long as time reaches minimumim (confirmed HIGH).
      // EVENT HAPPENED! Either the pin went LOW again (noise?) or it's a stable HIGH, i.e. end of pulse.

    //EXIT:
      if (millis() - tHigh >= T_MIN) { // Good pulse... ... Count this!
        pulses = pulses +1;
        if (pulses > MAX_PULSES) {reportError(-pulses); currentState = INIT;} // Too many pulses !! ??
        if (VERBOSE) {Serial.print("Ps:");Serial.println(pulses);}
        currentState = HI;
      } else {                       // Bad pulse... (noise)
        currentState = LO;
      }
    break;

    //---------------------------------------------
    case HI:
    //ENTRY:
      if (DEBUG) digitalWrite(STATUS_LED, HIGH);
      if (VERBOSE) Serial.println("H");

    // WAIT FOR EVENT:
      while (   (digitalRead(PULSE_INPUT) == HIGH)  // Wait while pin is stays HIGH (until it goes low)
             && (millis() - tHigh <= T_MAX)) {}; // as long as time does not exceed maximum.
      // EVENT HAPPENED! Either the pin went LOW again or something's wrong...

    //EXIT:
      if (millis() - tHigh >= T_MAX) { // If the pin stays high, that's the end of the pulse sequence. 
        reportPulses(pulses);
        currentState = INIT;
      } else {
        currentState = LO_CONFIRM;         // Otherwise there's (probably) another pulse (to be confirmed).
      }
    break;

    //---------------------------------------------
    case LO_CONFIRM:
    //ENTRY:
      tLow = millis(); // Save system time when pin went HIGH.
      if (VERBOSE) {Serial.print("LC -");Serial.println(millis() - tHigh);}

    // WAIT FOR EVENT:
      while (   (digitalRead(PULSE_INPUT) == LOW)     // Wait while pin is stays LOW
             && (millis() - tLow <= T_MIN)) {}; // as long as time reaches minimumim (confirmed LOW).
      // EVENT HAPPENED! Either the pin went HIGH again very quickly (noise?) or it's a stable LOW, i.e. a pulse.

    //EXIT:
      if (millis() - tHigh >= T_MIN) { // Stable low.
        currentState = LO;
      } else {                            // Bad pulse... Back to HI.
        currentState = HI;
      }
    break;

    default:
     if (VERBOSE) Serial.println("FELL INTO DEFAULT CASE!!!");
    break;
  };
};

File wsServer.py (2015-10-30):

#!/usr/bin/python
####################################################
# Name: Donation Box WebSockets deamon 
#
# Description:
# Provides the WebSockets Server which polls data from the DB, notifies any connected clients (browsers)
# and accepts messages (donations) from clients that then writes to the DB
#
# Author: Dimitris Koukoulakis
#
# License: GNU GPL v3.0
####################################################

from __future__ import print_function
import tornado.httpserver
import tornado.websocket
import tornado.ioloop
import tornado.web
import serial 
import MySQLdb 
import time
import threading
import datetime
import decimal
import json
import logging
from time import gmtime, strftime
from Adafruit_Thermal import *


#Init
json_data=open('config.json')
config = json.load(json_data)
json_data.close()
logging.basicConfig(filename='wsServer.log', level=logging.DEBUG, format='%(levelname)s %(asctime)s: %(message)s')
logging.debug('wsServer started')

coin = 0
#See the config.json file for the configuration
curr = config["General"]["currency"]
init_wait_time = config["General"]["Init Wait time (sec)"]
clients = []
dbserver = config["Database"]["server"]
dbuser = config["Database"]["username"]
dbpass = config["Database"]["password"]
dbname = config["Database"]["name"]

pr_enabled = config["Printer"]["enabled"]
pr_dev = config["Printer"]["dev"]
pr_baudrate = config["Printer"]["baudrate"]
pr_timeout = config["Printer"]["timeout"]
pr_feedlines = config["Printer"]["feedlines"]
pr_heattime = config["Printer"]["heattime"]

#wait at start up for mySQL to load
time.sleep(init_wait_time)

if pr_enabled:
  printer = Adafruit_Thermal(pr_dev, pr_baudrate, timeout=pr_timeout)

def Th_print(currency,value,name,email,prname,prid,donationid):
  if not pr_enabled:
    logging.debug('Thermal printer is disabled')
    return
    
  printer.begin(pr_heattime) 
  printer.setTimes(0,0) #print as fast as possible
  logging.debug('Printing donation to thermal printer')  
  printer.boldOn()
  printer.println('THANK YOU')
  printer.println(name)
  printer.boldOff()
  printer.print(value)
  printer.print(currency)
  printer.print(' to ')
  printer.print(prname)
  printer.println(' project')
  printer.println('Your donation registered')
  if email != '':
    printer.print('with ')
    printer.print(email)
     
  printer.feed(pr_feedlines)

  
def QueryDBonStart():	
  global dbserver
  global dbname
  global dbuser
  global dbpass
  global coin
  global curr

  #Connect to Database
  dbConn = MySQLdb.connect(dbserver,dbuser,dbpass,dbname) or die ("could not connect to database")
  cursor = dbConn.cursor()

  try:
    #print "Query DB...";
    #See if there are coins inserted that have not been donated
    sql = "SELECT currency,value,donationid FROM coinacceptor WHERE donationid < 0";
    cursor.execute(sql);
    # Get returned values
    for (currency,value,donationid) in cursor:
      #TODO: What should happen if one coin is of differenct currency?
      curr = currency
      coin += value
      logging.debug('DonationID: '+repr(donationid)+' Currency: '+repr(curr)+' Value: '+repr(coin))

    if coin != 0:
      # Send value and currency to web socket client
      send_donation(coin,curr)        
    cursor.close();  #close the cursor
  except MySQLdb.IntegrityError:
    logging.error('failed to fetch data')
  finally:
    cursor.close()  #close just incase it failed
  
  
def send_donation(c, msg):
  logging.debug('SEND: %s %s',str(c),msg)
  for client in clients:
    client.write_message(str(c)+msg)
  global coin
  global curr
  coin = 0
  curr = "EUR"


def send_project_total(pid, msg):
  logging.debug('PID|'+str(pid)+'|TOTAL|'+msg)
  for client in clients:
    client.write_message("PID|"+str(pid)+"|TOTAL|"+msg)


def QueryDB():
  LastTime = strftime("%Y-%m-%d %H:%M:%S", gmtime());
  while True:
    dbConn = MySQLdb.connect(dbserver,dbuser,dbpass,dbname) or die ("could not connect to database")
    cursor = dbConn.cursor()

    try:
      #print "Query DB...";
      sql = "SELECT timeinserted, value, currency FROM coinacceptor WHERE timeinserted > %s ORDER BY timeinserted DESC";
      #logging.debug('RUN SQL: SELECT timeinserted, value, currency FROM coinacceptor WHERE timeinserted > %s ORDER BY timeinserted DESC', LastTime)
      cursor.execute(sql,LastTime);

      data = cursor.fetchone();
      for (timeinserted, value, currency) in cursor:
        LastTime = timeinserted
        global coin
        coin = value
        global curr
        curr = currency
        logging.debug('%d %s', coin, curr)
        if coin != 0:
          send_donation(coin,curr)
      #print data
      cursor.close();  #close the cursor
    except MySQLdb.IntegrityError:
      logging.error('failed to fetch data')
    finally:
      cursor.close()  #close just incase it failed
    time.sleep(0.5);
    
    
def InsertDonation(currency,value,name,email,public, prname, prid):
  from time import gmtime, strftime
  timestamp = strftime("%Y-%m-%d %H:%M:%S", gmtime());
  dbConn = MySQLdb.connect(dbserver,dbuser,dbpass,dbname) or die ("could not connect to database")
  logging.debug('Insert donation to DB')
  dbConn.set_character_set('utf8')
  
  cursor = dbConn.cursor()
  
  cursor.execute('SET NAMES utf8;')
  cursor.execute('SET CHARACTER SET utf8;')
  cursor.execute('SET character_set_connection=utf8;')
  
  logging.debug('Name:'+name+' Email:'+email+' public:'+public+' Project Name:'+prname+' ProjectID:'+prid+' Currency:'+currency+' Value:'+value)
  if (public == 'false'):
    public = 0
  else:
    public = 1
  try:
    #Insert donation
    sql = "INSERT INTO donations (currency,ammount,projectname,email,name,public,projectid,timestamp) VALUES (%s,%s,%s,%s,%s,%s,%s,%s)"
    cursor.execute(sql,(currency,value,prname,email,name,public,prid,timestamp))
    dbConn.commit()
    #Get donation ID
    donationid = cursor.lastrowid
    #Update coins inserted with donation ID
    sql = "UPDATE coinacceptor SET donationid=%s WHERE donationid=-1"
    logging.debug('RUN SQL: UPDATE coinacceptor SET donationid=%s WHERE donationid=-1', donationid)
    cursor.execute(sql,donationid)
    dbConn.commit()
    cursor.close()
  except MySQLdb.IntegrityError:
    logging.error('failed to fetch data')
    for client in clients:
      client.write_message("ERROR")
  finally:
    cursor.close()  #close just incase it failed
    for client in clients:
      client.write_message("SUCCESS")
      logging.info('Data written successfuly')
  return donationid;
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

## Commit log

2015-09-28 Thermal printer support
2015-09-28 Added printer support
2015-09-30 Minor changes and new files added
    [donationbox.scad, front_panel.dxf, tablet-bottom-support.dxf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]
2015-10-01 Bill Of Materials
    [BOM.ods]
2015-10-01 Arduino code
2015-10-02 Electronics Schematics for DonationBox Raspberry Pi shield.
    [DonationBox.fzz]
2015-10-07 side_panel.svg: Added power socket.
2015-10-07 BlenderCAM for the right side panel
    * Blender file containing:
    - Imported (simplified) SVG side-panel.svg, extruded to correct depth.
    - CAM ops for 1/8-inch end-bit - 2.7mm effective cutting diameter.
    - Generated CAM paths.
    * Exported G-Code files for:
    - Groove, that holds front, back, top and bottom.
    - Cut-out of a hole for the IEC 60320 C14 power inlet / socket.
    [side.blend]
2015-10-07 Combined G-Code for side panel
    Concatenated socket, groove and cutout G-Codes
    in order to cut the side panel in a single run.
2015-10-08 Renamed side-panel to right-side-panel folder
    [side.blend]
2015-10-09 Added left side panel Blender and G-Code + renaming
    Produced a simplified SVG to import into blender, extruded 35cm and
    produced two G-Code files to round the upper corner cut-out piece.
    [back panel.blend, left-side panel.blend, right-side panel.blend]
2015-10-10 Corrected cutter diameter in back_panel.blend
    [back panel.blend]
2015-10-10 + bottom panel Blender + G-Code
    [bottom panel.blend]
2015-10-10 + front panel SVGs + Blender (part 1)
    [front panel.blend]
2015-10-10 Front panel part two (Blender + G-Codes)
    The printer-clamp-left an -right are optional to thin down the strength
    of the front plate, for use with the thermal printers, which can not
    clamp to any plates thicker than ca. 6mm.
    [front panel.blend]
2015-10-11 + top panel SVG and Blender (part 1)
    [top panel.blend]
2015-10-12 Top panel part 2 - middle plate (SVGs + Blender + G-Codes)
    [top panel.blend]
2015-10-12 Top panels part 3 - top plate (Blender + G-Codes)
    [top panel.blend]
2015-10-13 + top panel clamp (SVG, Blender and G-Code) & better top-top-slope
    [top panel.blend]
2015-10-13 + (left side) door (SVG, Blender and G-Code)
    This is intended for use with the piece of wood
    which is left from the cut-out of the left-side panel,
    which should be exactly 133mm wide [X] and 248mm high [Y].
    [door.blend]
2015-10-14 Updated BOM
    [BOM.ods]
2015-10-14 Reduced tablet clamp width to fit into top corner.
2015-10-14 + small piece to close gap at top rounding
    [rounding-gap.blend]
2015-10-14 + simple blocks of chipwood to screw door onto
    [door-hinge-blocks.blend]
2015-10-30 Added countdown timer

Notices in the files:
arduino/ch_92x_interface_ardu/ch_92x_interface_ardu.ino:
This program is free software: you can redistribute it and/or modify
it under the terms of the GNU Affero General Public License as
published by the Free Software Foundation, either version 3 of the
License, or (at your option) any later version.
